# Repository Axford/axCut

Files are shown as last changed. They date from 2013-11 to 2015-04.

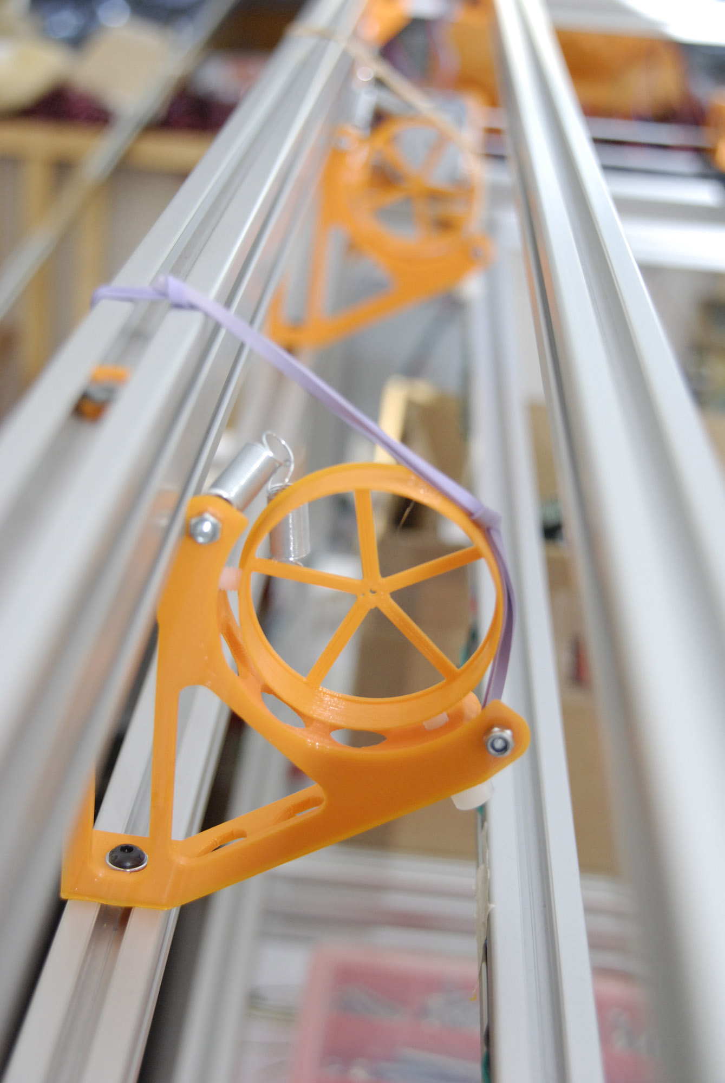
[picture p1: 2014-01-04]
images/wip_photos_1/_DSC1572.JPG

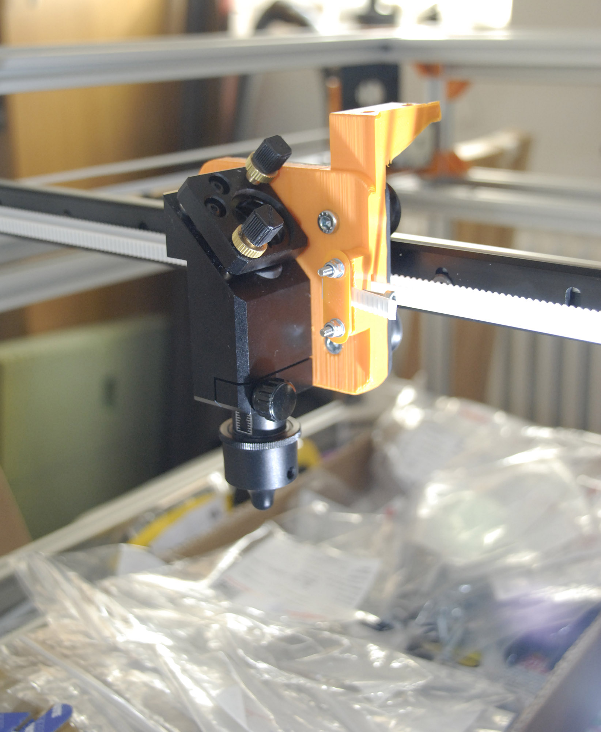
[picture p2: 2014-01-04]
images/wip_photos_1/_DSC1567.JPG

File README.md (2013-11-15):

axCut
=====

buildlog 2.x/Lasersaur inspired laser cutter

Clone the respository and open axCut.scad in latest version of OpenSCAD to view the WIP model.

Latest WIP image(s):

wip image

wip image

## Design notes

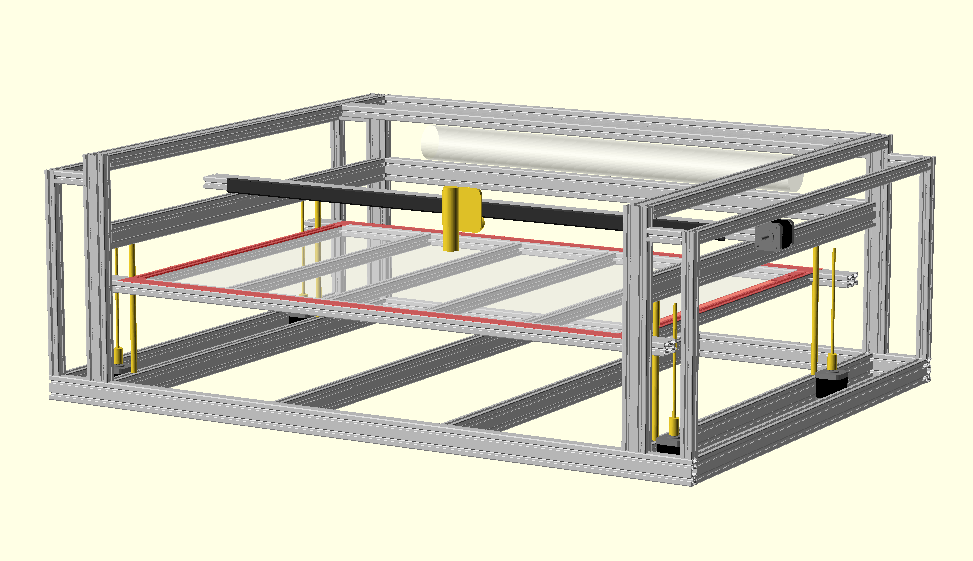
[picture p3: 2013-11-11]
images/axCut_wip1.png

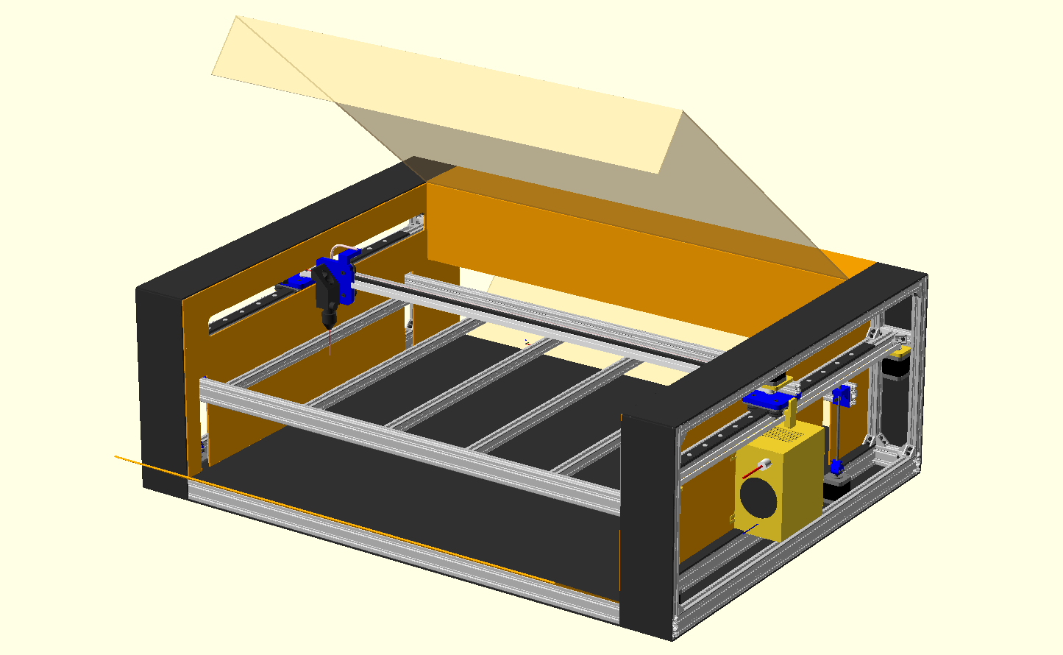
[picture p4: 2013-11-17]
images/axCut_wip8b.png

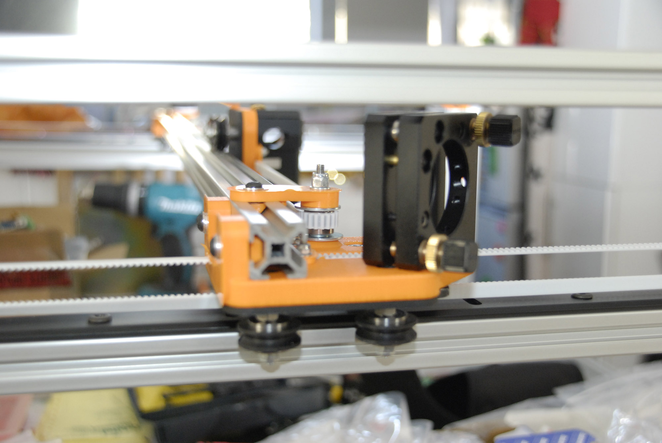
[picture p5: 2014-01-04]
images/wip_photos_1/_DSC1568.JPG

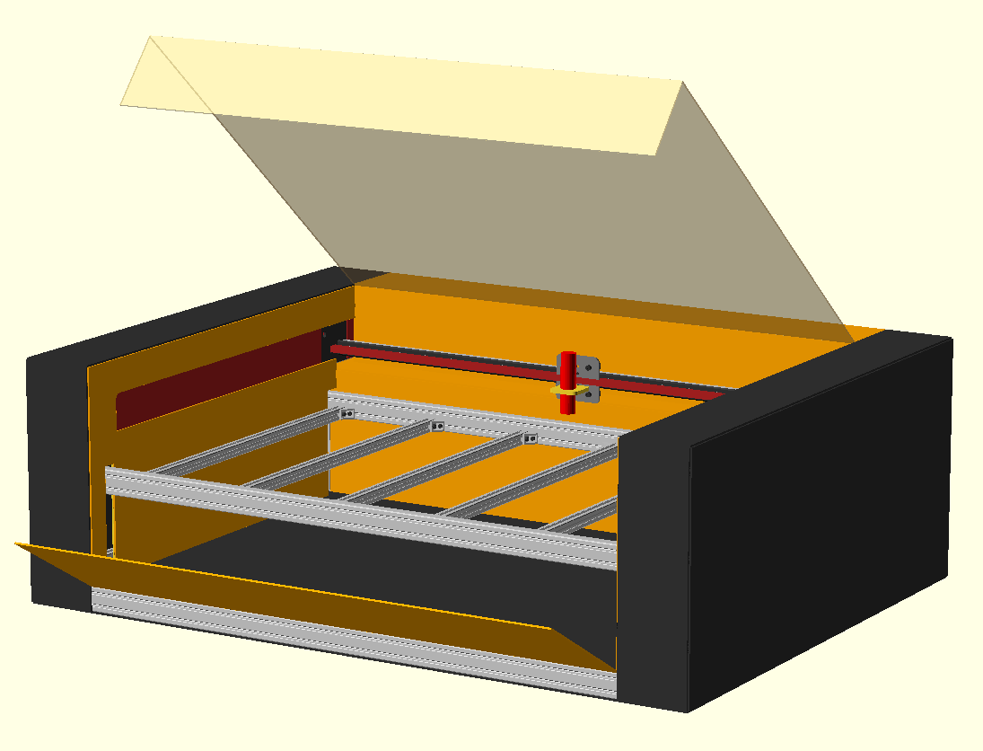
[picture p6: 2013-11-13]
images/axCut_wip4a.png

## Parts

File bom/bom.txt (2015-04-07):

Vitamins:
                  L                                        
                  a                                        
                  s                                        
                  e                                        
                  r                                        
                  b                                        
                  r                       Y                
              L   a                   Y   c                
              a   c                   c   a                
              s   k                   a   r                
              e   e                   r   r                
              r   t           X       r   i                
      C       a   a           c       i   a                
      l       s   s   T       a       a   g   Y            
      a       s   s   r       r       g   e           Z    
      d   F   e   e   o   X   r   X   e   r   i   Z   m    
      d   r   m   m   l   a   i   r   l   i   d   a   o   Z
  B   i   a   b   b   l   x   a   a   e   g   l   x   t   r
  e   n   m   l   l   e   i   g   i   f   h   e   e   o   o
  d   g   e   y   y   y   s   e   l   t   t   r   s   r   d
   |   |  8|   |   |   |   |   |   |   |   |   |   |   |   | 12 20x20TGusset:
   |   |  8|   |   |   |   |   |   |   |   |   |   |   |   |  8 20x40HeavyGusset:
   |   |   |   |   |   |   |   |  1|   |   |   |   |   |   |  1 Aluminium Extrusion BR_20x20 100mm
   |   |   |   |   |   |   |   |  1|   |   |   |   |   |   |  1 Aluminium Extrusion BR_20x20 1170mm
   |   |  8|   |   |   |   |   |   |   |   |   |   |   |   |  8 Aluminium Extrusion BR_20x20 350mm
  6|   |   |   |   |   |   |   |   |   |   |   |   |   |   |  6 Aluminium Extrusion BR_20x20 670mm
   |   |   |   |   | 10|   |   |   |   |   |   |   |   |   | 10 Aluminium Extrusion BR_20x20 710mm
   |   |  6|   |   |   |   |   |   |   |   |   |   |   |   |  8 Aluminium Extrusion BR_20x20 870mm
   |   |  3|   |   |   |   |   |   |   |   |   |   |   |   |  3 Aluminium Extrusion BR_20x20 990mm
  2|   |   |   |   |   |   |   |   |   |   |   |   |   |   |  2 Aluminium Extrusion BR_20x40 1100mm
   |   |   |   |   |  6|   |   |   |   |   |   |   |   |   |  6 Aluminium Extrusion BR_20x40 1160mm
   |   |  2|   |   |   |   |   |   |   |   |   |   |   |   |  2 Aluminium Extrusion BR_20x40 1200mm
   |   |   |   |   |  4|   |   |   |   |   |   |   |   |   |  4 Aluminium Extrusion BR_20x40 580mm
   |   |   |   |   |  4|   |   |   |   |   |   |   |   |   |  4 Aluminium Extrusion BR_20x40 670mm
   |   |  6|   |   |   |   |   |   |   |   |   |   |   |   |  6 Aluminium Extrusion BR_20x40 870mm
   |   |  1|   |   |   |   |   |   |   |   |   |   |   |   |  1 Aluminium Extrusion BR_20x40 990mm
 24|   |148|   |  4|   |   |   |  4|  2|  2|  4|   |   |   |196 Aluminium Extrusion Twist Nut
   |   |   |   |   |   |   |   |   |  2|   |  2|   |   |   |  4 Ball bearing 624 4mm x 13mm x 5mm
   |   |   |   |   |   |   |  8|   |   |  8|   |   |   |   | 16 Ball bearing 625_2RS 5mm x 16mm x 5mm
 12|   | 40|   |   |   |   |   |   |   |   |   |   |   |   | 52 BR20x20Gusset
   |   |   |   |   |   |   |   |  1|   |   |   |   |   |   |  1 Belt T2.5 x 6mm x 2185mm
   |   |   |   |   |   |   |   |   |   |   |   |   | 16|   | 16 M3 cap screw x 20mm
   |   |   |   |  4|   |   |   |  2|   |   |   |   |   |   | 10 M4 cap screw x 10mm
   |   |   |   |   |   |   |   |   |  2|  2|   |   |   |   |  4 M4 cap screw x 16mm
 24|   |148|   |   |   |   |   |  2|   |   |  4|   |   |   |182 M4 cap screw x 8mm
   |   |   |   |  4|   |   |   |   |   |   |   |   |   |   |  4 M5 cap screw x 20mm
   |   |   |   |   |   |   |  4|   |   |  4|   |   |   |   |  8 M5 cap screw x 25mm
   |   |   |   |   |   |   |  4|   |  4|  4|   |   |   |   | 12 M5 cap screw x 30mm
   |   |   |   |   |   |   |  4|   |   |  4|   |   |   |   |  8 DelrinVGrooveWheel:
   |   |   |   |   |   |   |  2|   |  4|  4|   |   |   |   | 10 M3 hex screw x 16mm
   |   |   |   |   |   |   |  2|   |   |   |   |   |   |   |  2 M3 hex screw x 25mm
   |   |   |   |   |   |   |  2|   |   |   |   |   |   |   |  2 M4 hex screw x 20mm
   |   |   |   |   |   |   |   |   |  1|   |  1|   |   |   |  2 M4 hex screw x 40mm
   |   |   |   |   |   |   |   | 20|   |   |   |   |   |   | 50 M5 low profile screw x 10mm
   |   |   |   |   |   |   |   |  1|   |   |   |   |  4|   |  7 NEMA17 x 47mm stepper motor
   |   |   |   |   |   |   |  4|   |  4|  4|   |   |   |   | 12 Nut M3
   |   |   |   |  4|   |   |   |   |   |   |   |   |   |   |  4 Nut M5
   |   |   |   |   |   |   |   |   |   |   |   |   | 16|   | 16 Nyloc nut M3
   |   |   |   |   |   |   |  2|   |  1|   |  1|   |   |   |  4 Nyloc nut M4
   |   |   |   |   |   |   |  4|   |   |  4|   |   |   |   |  8 Nyloc nut M5
   |   |   |   |   |   |   |  1|   |   |  1|   |   |   |   |  2 OpenRailPlate20:
   |   |   |   |   |   |   |  4|   |   |  4|   |   |   |   |  8 OpenRailSpacer:
   |   |   |   |   |   |   |   |  2|   |   |   |   |   |   |  2 Openrail1000:Openrail 1000mm
   |   |   |   |   |   |   |   |   |   |   |   |   |   |   |  4 Openrail750:Openrail 750mm
   |   |   |   |   |   |   |   | 20|   |   |   |   |   |   | 50 OpenrailTeeNut:
   |   |   |   |   |   |   |   |   |   |   |   |   |   |   |  1 Overall depth = ", 90
   |   |   |   |   |   |   |   |   |   |   |   |   |   |   |  1 Overall height = ", 38
   |   |   |   |   |   |   |   |   |   |   |   |   |   |   |  1 Overall width = ", 119
   |   |   |   |   |   |   |   |  4|   |   |   |   |   |   | 12 M3 pan screw x 8mm
   |   |   |   |   |   |   |   |  1|   |   |   |   |   |   |  3 T2.5x18 pulley 18 teeth
   |   |   |   |   |   |   |   |   |   |   |   |   |   |  2|  2 Smooth rod 10mm x 210mm
   |   |   |   |   |   |   |   |   |   |   |   |  2|   |   |  2 Rodlen", 21
   |   |   |   |   |   |   |   |   |   |   |   |   |  4|   |  4 Threaded rod M6 x 180mm
   |   |   |   |   |   |   |   |   |   |   |   |   |  4|   |  4 Neoprene tubing OD 8mm ID 5mm x 16mm
   |   |   |   |   |   |   |  4|  4|  4|  4|   |   | 16|   | 40 Washer M3 x 7mm x 0.5mm
   |   |  4|   |  4|   |   |  2|  4|  6|  2|  8|   |   |   | 38 Washer M4 x 9mm x 0.8mm
   |   |   |   |   |   |   |  4|   |   |  4|   |   |   |   |  8 Washer M5 x 10mm x 1mm
   |   |   |   |   |   |   |   |   |  2|   |  2|   |   |   |  4 Washer M5 x 20mm x 1.4mm
   |   |   |   |   |   |   |   |  4|   |   |   |   |   |   | 12 Star washer M3 x 0.5mm
   |   |   |   |   |   |   |   |   |   |   |   |   |   |   |  1 ", -38
   |   |   |   |   |   |   |   |   |   |   |   |   |   |   |  1 ", 37
   |   |   |   |   |   |   |   |   |   |   |   |   |   |   |  1 ", 42
   |   |   |   |   |   |   |   |   |   |   |   |   |   |   |  1 ", 50
   |   |   |   |   |   |   |   |   |   |   |   |   |   |   |  1 ", 8
   |   |   |   |   |   |   |  1|   |   |   |   |   |   |   |  1 laserHead:
   |   |   |   |   |   |   |   |  1|   |   |   |   |   |   |  2 laserMirror:
   |   |   |   |   |   |   |   |   |   |   |   |   |   |   |  1 ", 18

Printed:
   |   |   |   |   |   |   |   |   |   |   |   |   |   |   |  1 fixedMirrorHolder.stl
   |   |   |   |  2|   |   |   |   |   |   |   |   |   |   |  2 laserBracket.stl
   |   |   |   |   |   |   |  2|   |  2|  2|   |   |   |   |  6 xBeltClamp.stl
   |   |   |   |   |   |   |  1|   |   |   |   |   |   |   |  1 xBeltTensioner.stl
   |   |   |   |   |   |   |  1|   |   |   |   |   |   |   |  1 xCarriageBracket.stl
   |   |   |   |   |   |   |   |   |  1|   |   |   |   |   |  1 yCarriageBracketLeft.stl
   |   |   |   |   |   |   |   |   |   |  1|   |   |   |   |  1 yCarriageBracketRight.stl
   |   |   |   |   |   |   |   |   |   |   |  1|   |   |   |  1 y_idler_left.stl
   |   |   |   |   |   |   |   |   |   |   |  1|   |   |   |  1 y_idler_right.stl
   |   |   |   |   |   |   |   |   |   |   |   |   |  8|   |  8 z_coupling.stl

Sub-assemblies:
  1 bed
  1 cladding
  1 frame
  1 laserAssembly
  2 laserBracketAssembly
  1 trolley
  1 xAxis
  1 xCarriage
  1 xRail
  1 yCarriageLeft
  1 yCarriageRight
  1 y_idler_assembly
  1 zAxes
  4 zMotor
  2 zRod

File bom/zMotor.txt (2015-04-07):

zMotor:
Vitamins:
 16 M3 cap screw x 20mm
  4 NEMA17 x 47mm stepper motor
 16 Nyloc nut M3
  4 Threaded rod M6 x 180mm
  4 Neoprene tubing OD 8mm ID 5mm x 16mm
 16 Washer M3 x 7mm x 0.5mm

Printed:
  8 z_coupling.stl

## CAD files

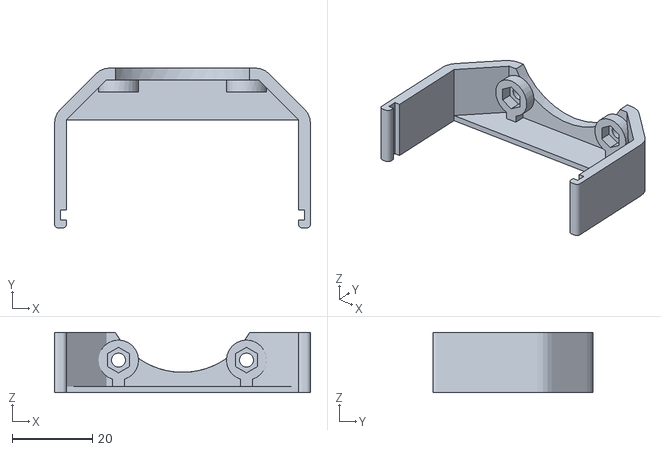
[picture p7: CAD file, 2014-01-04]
otherThings/Improved_ramps_fan.stl
64.0 x 40.0 x 15.0

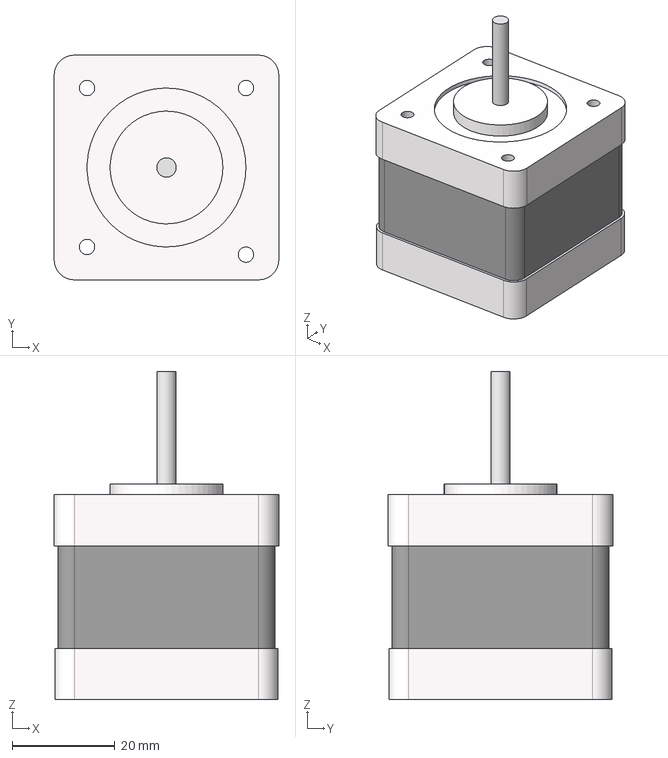
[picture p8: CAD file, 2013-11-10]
references/Nema17.stp
43.8 x 43.8 x 64.0 mm

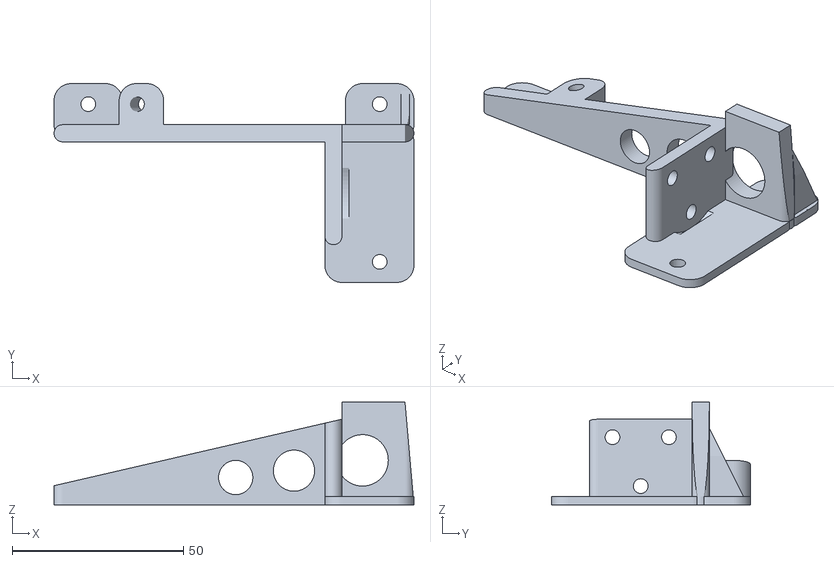
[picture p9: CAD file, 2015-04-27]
stl/upperFrameBracketForPistonLeft.stl
105.0 x 58.0 x 30.0

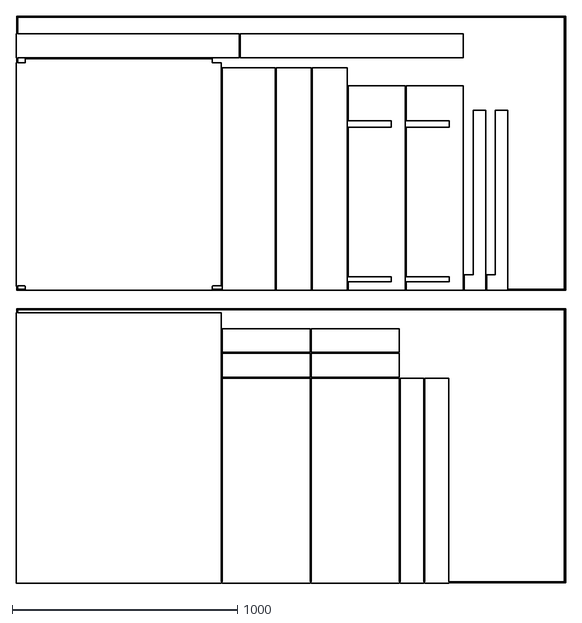
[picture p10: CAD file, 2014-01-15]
vitamins/claddingSheets.dxf
2440.0 x 2520.0

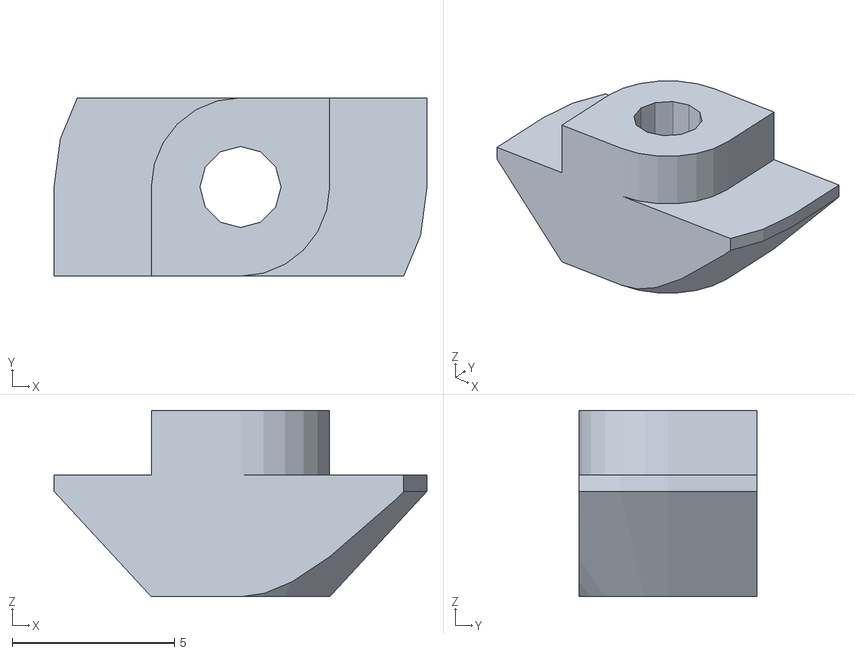
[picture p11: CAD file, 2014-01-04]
otherThings/hammerNut.stl
11.5 x 5.50 x 5.75

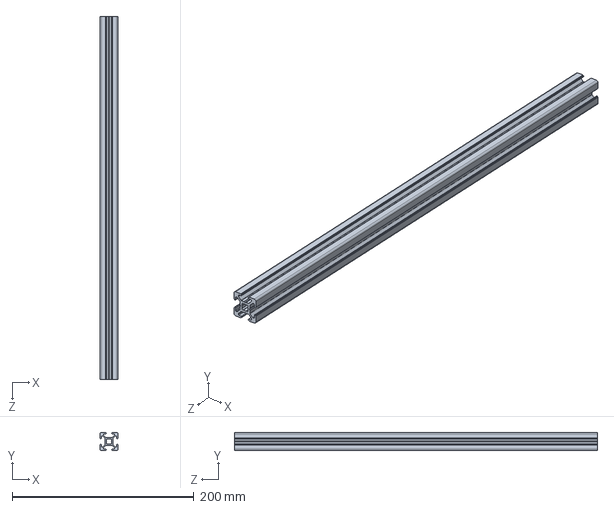
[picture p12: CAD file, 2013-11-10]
references/Rexroth-3 842 992 888_400MM.step
20.0 x 20.0 x 400.0 mm

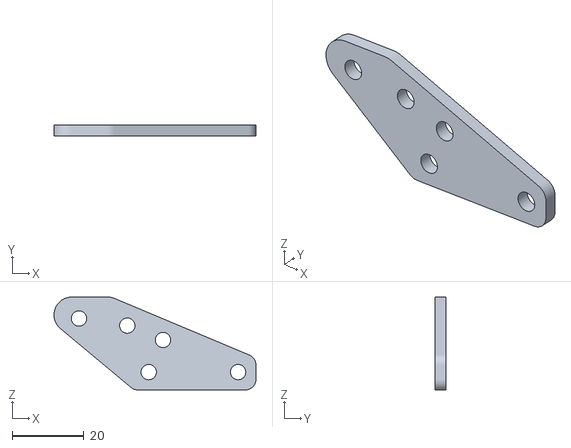
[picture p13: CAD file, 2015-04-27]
stl/ cableChainCarriageBracket.stl
56.5 x 3.00 x 26.0

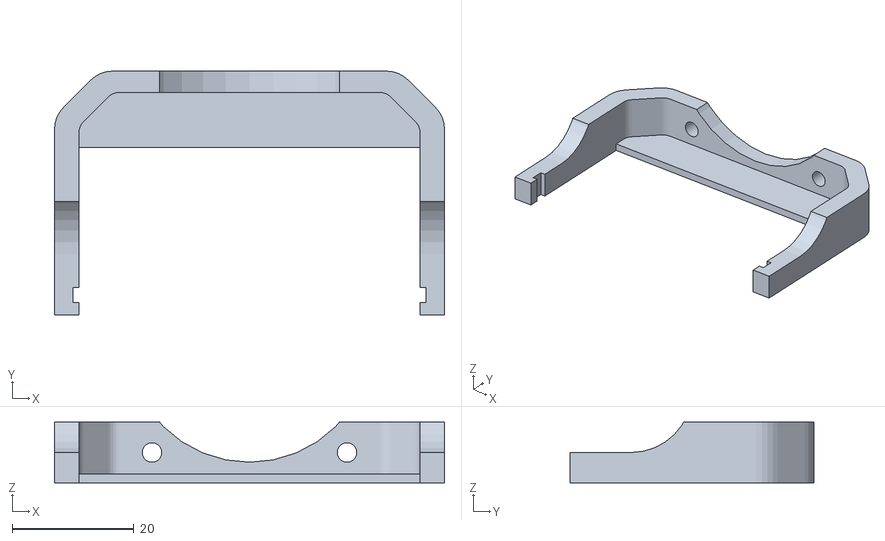
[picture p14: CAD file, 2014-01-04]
otherThings/rampsFanMount.stl
64.0 x 40.0 x 10.0

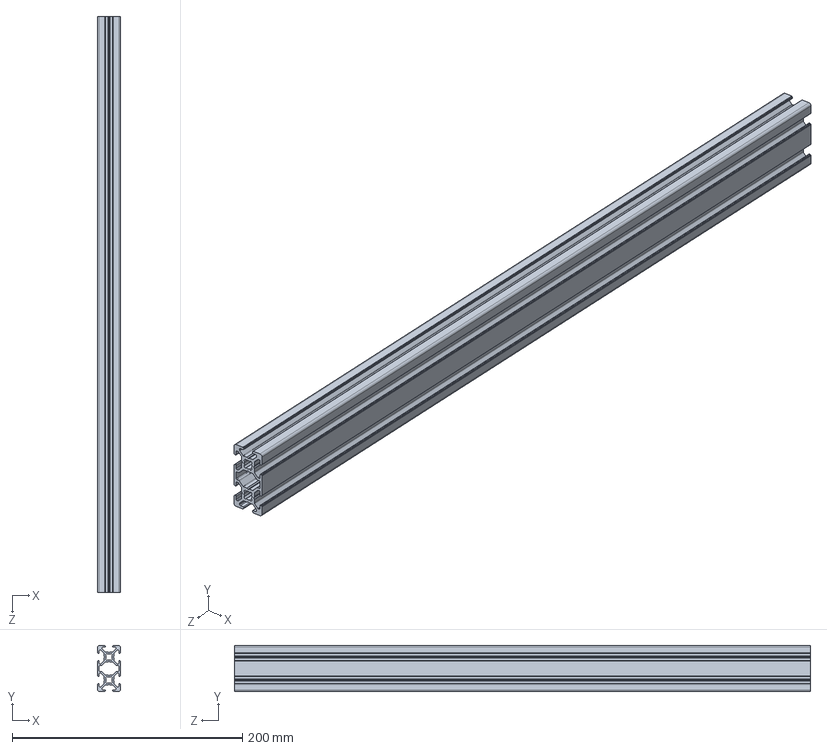
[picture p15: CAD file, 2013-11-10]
references/Rexroth-3 842 992 891_500MM.step
20.0 x 40.0 x 500.0 mm

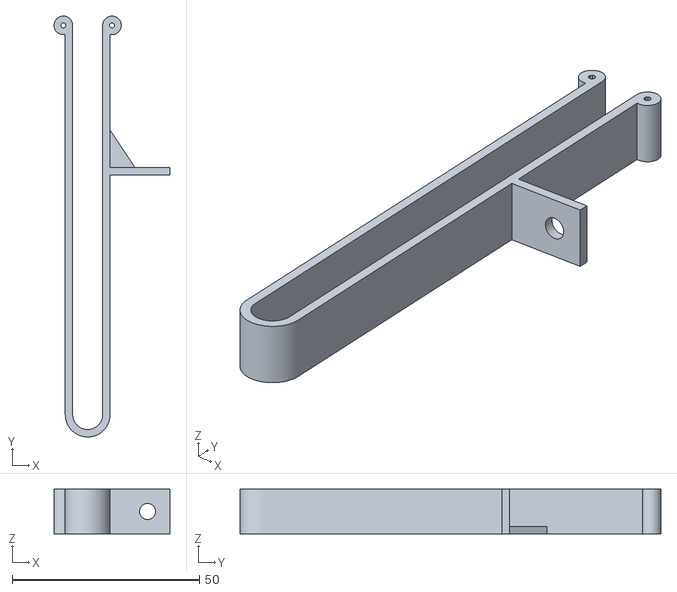
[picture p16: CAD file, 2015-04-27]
stl/airLineXBracket.stl
31.0 x 112.5 x 12.0

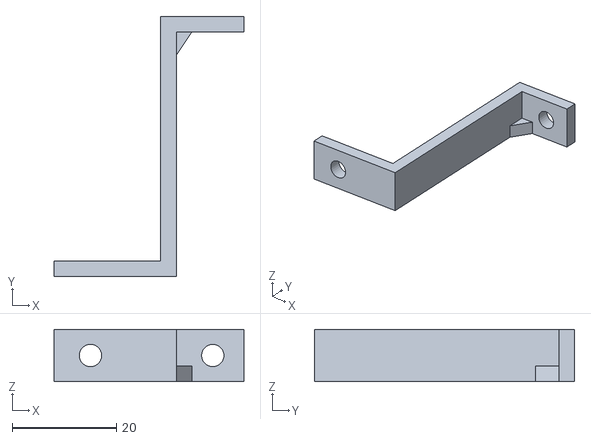
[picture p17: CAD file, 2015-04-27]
stl/cableChainXBracket.stl
36.5 x 50.0 x 10.0

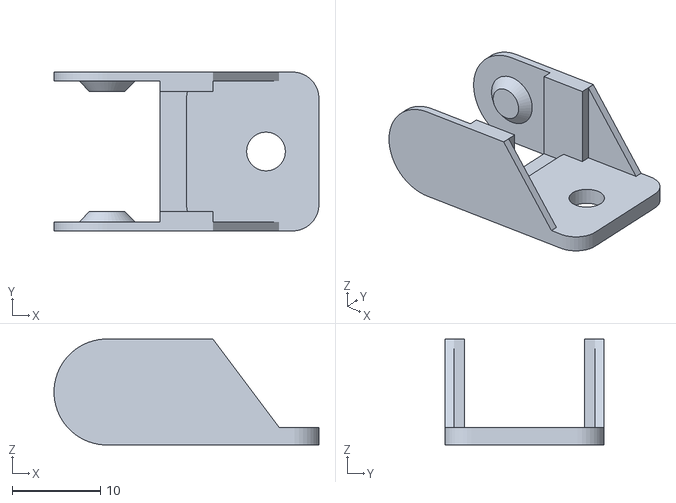
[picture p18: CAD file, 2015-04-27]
stl/cableChainFrameFixingMale.stl
30.0 x 18.0 x 12.0

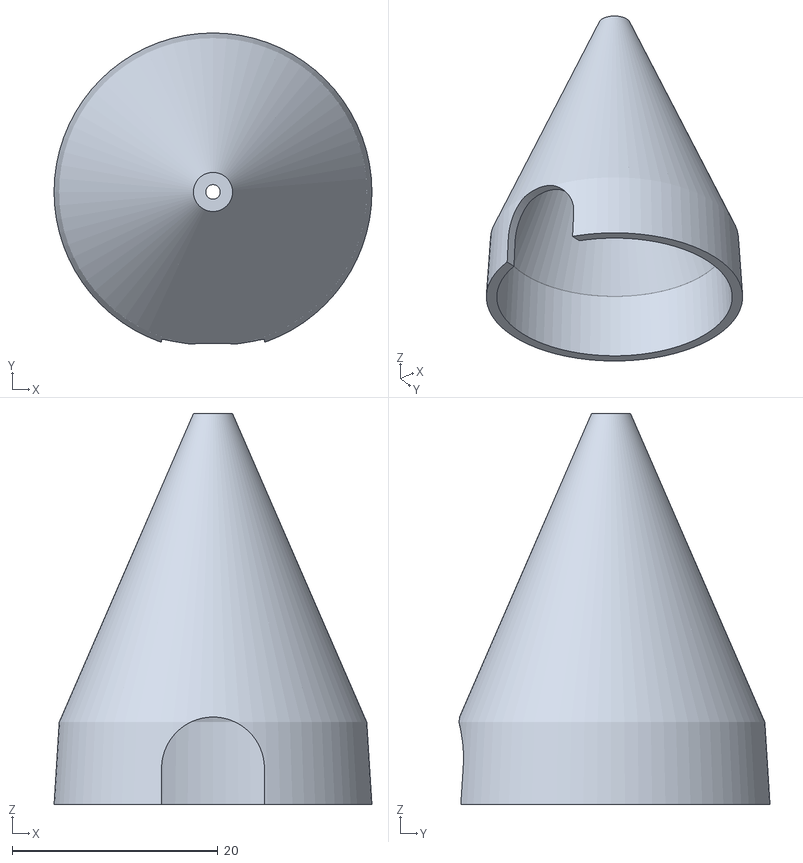
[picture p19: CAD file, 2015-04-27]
stl/laserNozzle.stl
30.9 x 30.2 x 38.0

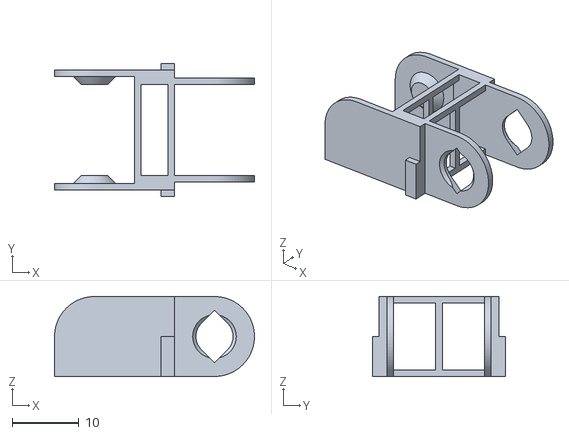
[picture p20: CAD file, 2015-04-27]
stl/cableChainLink.stl
30.0 x 20.0 x 12.0

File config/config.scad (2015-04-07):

//
// axCut
//
// GNU GPL v2
//
// Configuration file
//
bom = 0;                        // 0 no bom, 1 assemblies and stls, 2 vitamins as well
exploded = 0;                   // 1 for exploded view
simplify = false;    // reduces complexity of some parts, e.g. alu extrusions

show_jigs = true;               // show printed jigs required to build the machine
show_support = true;            // show support structures, must be set when generating STLs

debugConnectors = true;  //  show "attach" points

// Real-world colors for various parts & vitamins
use_realistic_colors = true;    // true for "real" colors, false for "distinct" colors (useful during design and for build instructions)
printed_plastic_color = "orange";
cable_strip_real_color = "fuchsia";
belt_real_color = "yellow";
bulldog_real_color ="black";

eta = 0.01;                     // small fudge factor to stop CSG barfing on coincident faces.
$fa = 5;
$fs = 0.5;

perim = 0.5;    // perim extrusion width for 0.2 or 0.3 layer height
layers = 0.3;
2perim = 2*perim;
4perim = 4*perim;

//
// Hole sizes
//
No2_pilot_radius = 1.7 / 2;       // self tapper into ABS
No4_pilot_radius = 2.0 / 2;       // wood screw into soft wood
No6_pilot_radius = 2.0 / 2;       // wood screw into soft wood

No2_clearance_radius = 2.5 / 2;
No4_clearance_radius = 3.5 / 2;
No6_clearance_radius = 4.0 / 2;

M2p5_tap_radius = 2.05 / 2;
M2p5_clearance_radius= 2.8 / 2;   // M2.5
M2p5_nut_trap_depth = 2.5;

M3_tap_radius = 2.5 / 2;
M3_clearance_radius = 3.3 / 2;
M3_nut_radius = 6.5 / 2;
M3_nut_trap_depth = 3;

M4_tap_radius = 3.3 / 2;
M4_clearance_radius = 2.2;
M4_nut_radius = 8.2 / 2;
M4_nut_trap_depth = 4;

M5_tap_radius = 4.2 / 2;
M5_clearance_radius = 5.3 / 2;
M5_nut_radius = 9.2 / 2;
M5_nut_depth = 4;

M6_tap_radius = 5 / 2;
M6_clearance_radius = 6.4 / 2;
M6_nut_radius = 11.6 / 2;
M6_nut_depth = 5;

M8_tap_radius = 6.75 / 2;
M8_clearance_radius = 8.4 / 2;
M8_nut_radius = 15.4 / 2;
M8_nut_depth = 6.5;

Z_screw_dia = 6;            // Studding for Z axis

//
// Feature sizes
//
default_wall = 4*perim;
thick_wall = 8*perim;

include <colors.scad>
include <utils.scad>
include <vitamins.scad>

endstop_wires    = [2, 1.4, "A"];   // 7 strands of 0.2
motor_wires      = [4, 1.4, "B"];
bed_wires        = [2, 2.8, "C"];   // 13A mains cable
fan_motor_wires  = [6, 1.4, "D"];   // fan and motor wires along top of gantry
two_motor_wires  = [8, 1.4,,"E"];   // Y and Z motors
thermistor_wires = endstop_wires;

endstop_wires_hole_radius = wire_hole_radius(endstop_wires);
motor_wires_hole_radius = wire_hole_radius(motor_wires);
two_motor_wires_hole_radius = wire_hole_radius(two_motor_wires);
fan_motor_wires_hole_radius = wire_hole_radius(fan_motor_wires);
bed_wires_hole_radius = wire_hole_radius(bed_wires);
thermistor_wires_hole_radius = wire_hole_radius(thermistor_wires);

cnc_sheets = false;                 // If sheets are cut by CNC we can use slots, etc instead of just round holes
base_nuts = false;                  // Need something under the base if using nuts
pulley_type = T2p5x18_metal_pulley;

Z_bearings = LM10UU;

X_motor = NEMA17;
Y_motor = NEMA17;
Z_motor = NEMA17;

X_belt = T2p5x6;
Y_belt = T2p5x6;

motor_shaft = 5;

Z_nut_radius = M6_nut_radius;
Z_nut_depth = M6_nut_depth;
Z_nut = M6_nut;

//
// Default screw use where size doesn't matter
//
cap_screw = M3_cap_screw;
hex_screw = M3_hex_screw;
//
// Screw for the frame and base
//
frame_soft_screw = No6_screw;               // Used when sheet material is soft, e.g. wood
frame_thin_screw = M4_cap_screw;            // Used with nuts when sheets are thin
frame_thick_screw = M4_pan_screw;           // Used with tapped holes when sheets are thick and hard, e.g. plastic or metal


screw_clearance_radius = screw_clearance_radius(cap_screw);
nut = screw_nut(cap_screw);
nut_radius = nut_radius(nut);
nut_trap_depth = nut_trap_depth(nut);
washer = screw_washer(cap_screw);

belt_clearance = 0.2;                   // clearance of belt clamp slots

Z_bar_dia = Z_bearings[2];

Y_idler_bearing = BB624;
X_idler_bearing = BB624;



///  

// OpenRail lengths  1000, 750

bedM = 30;  // bed margin, applied all round

bedW = 1000 - ORPlateWidth(ORPLATE20)/2 - 2*bedM;  //  adjusted to make full use of 1000mm rails
bedD = 750 - ORPlateWidth(ORPLATE20)/2 - 2*bedM;  // adjusted to make full use of 750mm rails

bedH = 300;
bedO = 70;  //bedOvershoot - applies to width only

bedWM = bedW + 2*bedM;  // with margins
bedDM = bedD + 2*bedM;

bedRibs = 6;  // number of ribs (along y axis)

bedVPos = 200;

zTravel = 210;

yCarriagePos = +bedD/2 -300;   // +-bedD
xCarriagePos = -bedW/2;    // +-bedW

xO = 60;  // xOvershoot
xVPos = 300;  // height of x axis above datum
yVPos = 270;  // height of y axis - to centreline of 2040 profile

rightW = 120;  // width of right casing, excludes outer panelling, runs from edge of bed margin
leftW = rightW;
backD = 150;  // depth of back casing
frontD = 40;  // depth of front casing

claddingC = 5;  // cladding clearance, inc thickness
claddingT = 3;  // cladding thickness


// frame centre lines, x/y relative to centre of bed, base of frame at z=0
//  centres lines lying in x axis
frameCX = [-bedDM/2 - frontD+10,
			bedDM/2 + claddingC + 10,  // back of bed
			bedDM/2 + claddingC + 60,  // behind x axis
			bedDM/2 + backD];

//  centres lines lying in y axis
frameCY = [-bedWM/2-rightW+10,  
		   -bedWM/2- 65,   // y rail
		   -bedWM/2 - claddingC-20,   
		   bedWM/2 + claddingC + 20,
		   bedWM/2 + 65,   // y rail
           bedWM/2 + leftW-10];     
           
//  centres lines lying in z axis
frameCZ = [20, 
		   zTravel + 50,   //  top of z rails	
           zTravel + 65,   //  y rails
		   zTravel + 170,   // outer corners
           zTravel + 170];  // top


showSealingBelts = false;

bedBearingOffset = 40;    // distance from centreline of front rail to centreline of rod
bedMotorYOffset = 40;  // distance from centreline of front/back rails to centreline of motor

showLaserBeam = true;


// trolley
trolleyHeight = 600;  // height from floor to top of trolley
trolleyDepth = 760;  // outer dimensions, excluding cladding
trolleyFloorClearance = 20;  // height above floor, to allow room for levelling feet


echo("Overall width = ", (frameCY[5]-frameCY[0]+16));
echo("Overall depth = ", (frameCX[3]-frameCX[0]+16));
echo("Overall height = ", (frameCZ[4]-frameCZ[0]+26));

for (i=[0:3])
	echo("X centres: ", frameCX[i]);


include <assemblies.scad>

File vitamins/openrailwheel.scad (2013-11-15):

// OpenRail delrin or steel wheel
// drawn by jdausilio/zeke7237

// from openbuilds drawings
openrailwheel_minRadius=18.75/2;
openrailwheel_coneMajorRadius=24.39/2;
openrailwheel_coneMinorRadius=9.77;
openrailwheel_width=10.23;
openrailwheel_vWidth=4.84;
openrailwheel_vGap=0.55;
openrailwheel_holeRadius=15.75/2;
openrailwheel_ridge=13.89/2;

module v_cone() {
	cylinder(r1=openrailwheel_coneMinorRadius,r2=openrailwheel_coneMajorRadius,h=openrailwheel_vWidth/2, center=true);
}

module openrail_eccentric_spacer() {
	vitamin(str("OpenRailEccentricSpacer:"));
	
	color(grey80)
		render()
		tube(8/2,5/2,5,$fn=6,center=false);
}

module openrail_spacer() {
	vitamin(str("OpenRailSpacer:"));
	
	color(grey80)
		render()
		tube(7/2,5/2,5,center=false);
}

module openrail_wheel() {
	vitamin(str("DelrinVGrooveWheel:"));

	color(grey20)
	render()
	difference() {
		union() {
			difference() {
				union() {
					cylinder(r=openrailwheel_minRadius, h=openrailwheel_width, center=true);
					translate([0,0,openrailwheel_vWidth/2+openrailwheel_vGap/2])cylinder(r=openrailwheel_coneMinorRadius, h=openrailwheel_vWidth, center=true);
					translate([0,0,-openrailwheel_vWidth/2-openrailwheel_vGap/2])cylinder(r=openrailwheel_coneMinorRadius, h=openrailwheel_vWidth, center=true);
					translate([0,0,openrailwheel_vGap/2+openrailwheel_vWidth/4])v_cone();
					translate([0,0,openrailwheel_vGap/2+openrailwheel_vWidth/4+openrailwheel_vWidth/2])rotate([180,0,0])v_cone();
					translate([0,0,-(openrailwheel_vGap/2+openrailwheel_vWidth/4)])rotate([180,0,0])v_cone();
					translate([0,0,-(openrailwheel_vGap/2+openrailwheel_vWidth/4+openrailwheel_vWidth/2)])v_cone();
				}
				cylinder(r=openrailwheel_holeRadius,h=20,center=true);
			}
			cylinder(r=openrailwheel_holeRadius+1,h=1,center=true);
		}
		cylinder(r=openrailwheel_ridge,h=5,center=true);
	}
}

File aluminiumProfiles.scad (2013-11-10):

//  Modules for the Bosch Rexroth series of aluminium profiles
//  Sourced from http://www.kjnltd.co.uk/
//  
//  Author - Damian Axford
//  Public Domain

use <moreShapes.scad>

eta = 0.01;


// Bore Types
BR_20x20_Bore = [5.5, 1.5, 7];

function aluProBore_r(boreType) = boreType[0]/2;
function aluProBore_outsetW(boreType) = boreType[1];
function aluProBore_outsetR(boreType) = boreType[2]/2;

// Core Types
BR_20x20_Core = [9,2,0.75];

function aluProCore_w(coreType) = coreType[0];
function aluProCore_keyW(coreType) = coreType[1];
function aluProCore_keyD(coreType) = coreType[2];

//Corner Types
BR_20x20_Corner = [20, 7, 1.5, 0.5, 4];

// Side Types  - for closed slots
BR_20x20_Side = [20, 1.5];

// Side Styles
BR_0 = [0,0,0,0];
BR_1S = [0,1,1,1];
BR_2S = [0,1,0,1];
BR_3S = [0,1,0,0];
BR_2SA = [1,1,0,0];

// Profiles - combination of elements

BR_20x20 = [BR_20x20_Bore, BR_20x20_Core, BR_20x20_Corner, BR_20x20_Side, BR_0, 1, 1];
BR_20x20_1S = [BR_20x20_Bore, BR_20x20_Core, BR_20x20_Corner, BR_20x20_Side, BR_1S, 1, 1];
BR_20x20_2S = [BR_20x20_Bore, BR_20x20_Core, BR_20x20_Corner, BR_20x20_Side, BR_2S, 1, 1];
BR_20x20_3S = [BR_20x20_Bore, BR_20x20_Core, BR_20x20_Corner, BR_20x20_Side, BR_3S, 1, 1];
BR_20x20_2SA = [BR_20x20_Bore, BR_20x20_Core, BR_20x20_Corner, BR_20x20_Side, BR_2SA, 1, 1];

BR_20x40 = [BR_20x20_Bore, BR_20x20_Core, BR_20x20_Corner, BR_20x20_Side, BR_0, 1, 2];

BR_20x60 = [BR_20x20_Bore, BR_20x20_Core, BR_20x20_Corner, BR_20x20_Side, BR_0, 1, 3];

BR_20x80 = [BR_20x20_Bore, BR_20x20_Core, BR_20x20_Corner, BR_20x20_Side, BR_0, 1, 4];

//twistLockNutType

BR_20x20_TwistLockNut = [5.8,11.3,4,0.8,1.5];


module aluProBore(boreType, $fn=16) {
	union() {
		circle(r=aluProBore_r(boreType));
	
		intersection() {
			circle(r=aluProBore_outsetR(boreType));
			for (i=[0:3]) 
				rotate([0,0,i*90 + 45]) 	
				square([aluProBore_outsetR(boreType)*2,aluProBore_outsetW(boreType)], center=true);
		}
	}
}


module aluProCore(coreType) {
	w = aluProCore_w(coreType);
	keyW = aluProCore_keyW(coreType);
	keyD = aluProCore_keyD(coreType);

	difference() {
		square([w,w],center=true);

		// remove keys
		for (i=[0:3]) 
			rotate([0,0,i*90])
			translate([w/2,0,0])
			polygon([[eta,keyW/2], 
                      [-keyD,0], 
                      [eta,-keyW/2]]); 
	}
}


module aluProCorner(cornerType, $fn=8) {
	// xy corner
	w1 = cornerType[0];
	w2 = cornerType[1];
	t = cornerType[2];
	cham = cornerType[3];
	w3 = cornerType[4];	

	union() {	
		// radial arm
		rotate([0,0,45]) translate([0,-t/2,0]) square([w1/2+t,t]);

		// outer radius
		translate([w1/2-t,w1/2-t,0]) circle(r=t);

		// corner block
		translate([w1/2-w3,w1/2-w3]) square([w3-t+eta,w3-t+eta]);

		// returns
		for (i=[0,1]) mirror([i,i,0]) {
			translate([w1/2-w2,w1/2-t,0]) square([w2-t,t-cham]);
			translate([w1/2-w2+cham,w1/2-cham-eta,0]) square([w2-t-cham,cham+eta]);
		}
	}
}

module aluProSide(sideType) {
	// x side
	w = sideType[0];
	t = sideType[1];
	translate([w/2-t-eta,-w/4,0]) square([t+eta,w/2]);	
}

module aluProHollow(cornerType) {
	// x hollow
	w1 = cornerType[0];
	t = cornerType[2];
	w3 = cornerType[4];	

	translate([w1/2,0]) square([2*w3 - 2*t, w1 - 2*t],center=true);
}

// TSlot - to be unioned onto a printed part for engaging tightly with the aluprofile
//  same centre and orientation as a full profile section, x+ side
// protrudes eta beyond external boundary of section to allow for union
// requires linear_extrude'ing
module aluProTSlot(profileType, $fn=8) {
	//BR_20x20_Corner = [20, 7, 1.5, 0.5, 4];
	//BR_20x20_Core = [9,2,0.75];
	
	coreType = profileType[1];
	cornerType = profileType[2];
	 
	w1 = cornerType[0];
	w2 = cornerType[1];
	t = cornerType[2];
	cham = cornerType[3];
	w3 = cornerType[4];	

	tol = 0.5;  // mm tolerance, total per gap

	slotW = w1- 2*w2 - tol;
	slotD = (w1 - coreType[0]) / 2 - tol;
	slotOffset = coreType[0]/2 + tol;
	
	wingW = w1 - 2*w3 - 4*tol;
	wingInset = t + tol/2;

	union() {	
		// central block
		translate([slotOffset,-slotW/2,0]) square([slotD+eta, slotW]);
	
		// wings
		for (i=[0,1]) mirror([0,i,0]) {
			polygon(points=[[slotOffset,slotW/2],[w1/2-w3/2-tol,wingW/2],[w1/2-wingInset,wingW/2],[w1/2-wingInset, slotW/2]], paths=[[0,1,2,3]]);
		}
	}
}

// TSlotLug - to be unioned onto a printed part for engaging tightly with the aluprofile slot
//  same centre and orientation as a full profile section, x+ side
// protrudes eta beyond external boundary of section to allow for union
// NB: solid part
module aluProTSlotLug(profileType, l=5, $fn=8) {
	//BR_20x20_Corner = [20, 7, 1.5, 0.5, 4];
	//BR_20x20_Core = [9,2,0.75];
	
	coreType = profileType[1];
	cornerType = profileType[2];
	 
	w1 = cornerType[0];
	w2 = cornerType[1];
	t = cornerType[2];
	cham = cornerType[3];
	w3 = cornerType[4];	

	tol = 0.5;  // mm tolerance, total per gap

	slotW = w1- 2*w2 - tol;
	slotD = (w1 - coreType[0]) / 2 - tol;
	slotD2 = l < slotD ? l : slotD;
	slotOffset = coreType[0]/2 + tol;
	
	wingW = w1 - 2*w3 - 4*tol;
	wingInset = t + tol/2;

	union() {	
		// central block
		translate([slotOffset,-slotW/2,0]) square([slotD2+eta, slotW]);
	}
}



module aluProBasicSection(profileType) {
	difference() {
		union() {
			aluProCore(profileType[1]);
			
			for (i=[0:3]) rotate([0,0,i*90]) {
				aluProCorner(profileType[2]);

				if (profileType[4][i] == 1)
					aluProSide(profileType[3]);
			}
		}
		aluProBore(profileType[0]);
	}
}

module aluProSection(profileType) {
	x = profileType[5];
	y = profileType[6];
	w = profileType[3][0];
	sx = -(x-1)*w/2;
	sy = -(y-1)*w/2;

	difference() {
		union() {
			for (i=[0:x-1])
				for (j=[0:y-1])
					translate([sx + w * i, sy + w * j,0]) aluProBasicSection(profileType);
			
			// fill-in sides
			if (y > 1)
				for (i=[0:y-2])
					for (j=[0,1]) 
						mirror([j,0,0])
							translate([sx + (x-1) * w/2, sy + i*w + w/2,0])
								aluProSide(profileType[3]);
		}

		// remove hollows
		if (y > 1)
			for (i=[0:y-2])
				for (j=[0,1]) 
					mirror([j,0,0])
						translate([sx + (x-1) * w/2, sy + i*w,0])
							rotate([0,0,90]) aluProHollow(profileType[2]);
	}
		
}

module aluProExtrusion(profileType, l=100, center=false) {
	color([0.8,0.8,0.8])
	    translate([0,0,center?-l/2:0]) 
		linear_extrude(height=l)
		aluProSection(profileType, center);
}

//BR_20x20_TwistLockNut = [5.8,11.3,4,0.8,1.5];
// aligned such that the origin is level with the surface of the profile when the nut is locked
module aluProTwistLockNut(tlnt) {
	color("silver")
	translate([0,0,-tlnt[2] -tlnt[3] - (tlnt[4] - tlnt[3])]) 
	difference() {
		union() {
			translate([0,0,tlnt[2]-0.5-eta]) cube([tlnt[1],tlnt[0],1+2*eta],center=true);
			translate([0,0,(tlnt[2]-1)/2]) rotate([90,0,0]) trapezoidPrism(tlnt[1],tlnt[0],tlnt[2]-1,-(tlnt[1] - tlnt[0])/2,tlnt[0],center=true);
			
			translate([0,0,tlnt[3]/2 + tlnt[2]-eta]) cube([tlnt[0],tlnt[0],tlnt[3] + eta],center=true);
		}
	
		translate([0,0,-1]) cylinder(h=20, r=tlnt[2]/2, $fn=8);
	}
}

*arrangeShapesOnGrid(showLocalAxes=true) {
	aluProExtrusion(BR_20x20, l=80, center=true);
	aluProExtrusion(BR_20x20_1S, l=50);
	aluProExtrusion(BR_20x20_2S, l=50);
	aluProExtrusion(BR_20x20_3S, l=70);
	aluProExtrusion(BR_20x20_2SA, l=70);

	aluProExtrusion(BR_20x40, l=70, center=false);
	aluProExtrusion(BR_20x60, center=true);
	rotate([0,0,35]) aluProExtrusion(BR_20x80, center=false);
}

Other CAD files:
stl/upperFrameBracketLeft.stl
stl/exhaustCoupling.stl
stl/upperFrameBracketForPiston.stl
stl/upperFrameBracketForHingeLeft.stl
axCut.scad
assemblies/CableChainv3.scad
assemblies/bed.scad
assemblies/cableChain.scad
assemblies/cladding.scad
assemblies/cooling.scad
assemblies/electronics.scad
assemblies/exhaust.scad
assemblies/frame.scad
assemblies/laser.scad
assemblies/trolley.scad
assemblies/xAxis.scad
assemblies/xLimitSwitch.scad
assemblies/yAxes.scad
assemblies/yIdler.scad
assemblies/z-coupling.scad
assemblies/zAxes.scad
assemblies/zLimitSwitch.scad
ball-bearings.scad
bom.scad
claddingSheets.scad
config/assemblies.scad
config/bom.scad
config/colors.scad
config/utils.scad
config/vitamins.scad
curvedPipe.scad
microbore.scad
microswitch.scad
otherThings/uploads-0c-e6-5b-80-5a-RAMPS+Fan+Mount.scad
otherThings/uploads-5d-4e-60-6e-da-T-Nut.scad
partdev.scad
partdev2.scad
screws.scad
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

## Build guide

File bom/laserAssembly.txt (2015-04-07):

laserAssembly:
Vitamins:

Printed:

Sub-assemblies:
  2 laserBracketAssembly

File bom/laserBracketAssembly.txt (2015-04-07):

laserBracketAssembly:
Vitamins:
  4 Aluminium Extrusion Twist Nut
  4 M4 cap screw x 10mm
  4 M5 cap screw x 20mm
  4 Nut M5
  4 Washer M4 x 9mm x 0.8mm

Printed:
  2 laserBracket.stl

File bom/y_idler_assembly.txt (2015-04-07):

y_idler_assembly:
Vitamins:
  4 Aluminium Extrusion Twist Nut
  2 Ball bearing 624 4mm x 13mm x 5mm
  4 M4 cap screw x 8mm
  1 M4 hex screw x 40mm
  1 Nyloc nut M4
  8 Washer M4 x 9mm x 0.8mm
  2 Washer M5 x 20mm x 1.4mm

Printed:
  1 y_idler_left.stl
  1 y_idler_right.stl

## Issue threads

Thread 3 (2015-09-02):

Where's the license

burdickjp, 2015-09-02:
Your laser cutter looks awesome, but I don't see a license anywhere on the repo. Am I missing something?

I use the CERN license following OSHWA guidelines for my open source hardware projects.
http://www.ohwr.org/projects/cernohl/wiki

Axford, 2015-09-02:
thanks ... and forgot to add one when I first uploaded the repo - treat as public domain!

Will upload a statement to that effect at some point

thanks
D

burdickjp, 2015-09-02:
If it is no different to you, use a license which guarantees derivative work is also free by adopting an open hardware license. Public domain does not guarantee this, and can be detrimental to the community.
Just upload the cern license and continue about your day. You won't see the difference, but we (the community) will!
http://www.ohwr.org/attachments/2388/cern_ohl_v_1_2.txt

Axford, 2015-09-04:
I'm fairly indifferent...  CERN license sounds ok, will add when near a suitable computer

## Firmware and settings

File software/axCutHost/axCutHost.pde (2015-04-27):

import processing.serial.*;
import controlP5.*;
import java.util.Arrays;
import java.io.BufferedWriter;
import java.io.FileWriter;

ControlP5 cp5;
PFont f;

DropdownList dlSerialPorts;
StringList serialLog;
Serial port; 

JSONObject config;

float x=0, y=0, z=0;

String lastCmd = "";
String lastCmdRaw = "";
int lastLineNo = 0;
int resendCount = 0;

StringList sendBuffer = new StringList();

boolean cts = true;
boolean resend = false;

void saveConfig() {
  // save connection string
  saveJSONObject(config, "config.json");
}

void stop() {
  saveConfig(); 
  Disconnect(0);

  super.stop();
}


void setup() {
  size(700, 400, P3D);
  f = createFont("Arial", 11, true); 

  try {
    config = loadJSONObject("config.json");
  } 
  catch(Exception e) {
  }

  cp5 = new ControlP5(this);

  // Configure Serial Ports Dropdown
  // -------------------------------
  dlSerialPorts = cp5.addDropdownList("dlSerialPorts")
    .setPosition(5, 25)
      .setWidth(200)
        ;
  dlSerialPorts.captionLabel().set("Choose a Serial Port");
  customize(dlSerialPorts);
  // Get list of ports
  dlSerialPorts.addItems(Serial.list());

  if (config != null) {
    int i = Arrays.asList(Serial.list()).indexOf(config.getString("port"));  
    dlSerialPorts.setValue(i);
  }

  // Connect button
  cp5.addButton("Connect")
    .setPosition(220, 5)
      .setSize(50, 20)
        ;

  // Disconnect button
  cp5.addButton("Disconnect")
    .setPosition(280, 5)
      .setSize(50, 20)
        ;


  // home
  cp5.addButton("Home")
    .setPosition(340, 5)
      .setSize(50, 20)
        ;


  // Send
  cp5.addButton("SendCommand")
    .setPosition(400, 5)
      .setSize(50, 20)
        ;
        
        
  // Store
  cp5.addButton("Store")
    .setPosition(460, 5)
      .setSize(50, 20)
        ;
        
        
   // PlayBack
  cp5.addButton("PlayBack")
    .setPosition(520, 5)
      .setSize(50, 20)
        ;
        
   // Abort
  cp5.addButton("Abort")
    .setPosition(580, 5)
      .setSize(50, 20)
        ;
        
  // Z
  cp5.addSlider("Z")
    .setValue(0.0)
      .setRange(0.0, 300.0)
        .setPosition(220, 170)
          .setSize(200, 20)
            ; 

  cp5.addTextfield("LastCommand")
    .setPosition(220, 200)
      .setSize(400, 20)
        .setFont(createFont("arial", 11))
          .setAutoClear(false)
            ;

  cp5.addTextfield("NewCommand")
    .setPosition(220, 250)
      .setSize(400, 20)
        .setFont(createFont("arial", 11))
          .setAutoClear(false)
            ;
            
  cp5.addTextfield("ResendErrors")
    .setPosition(220, 290)
      .setSize(40, 20)
        .setFont(createFont("arial", 11))
          .setAutoClear(false)
            ;
            
  // Arm button
  cp5.addButton("ArmLaser")
    .setPosition(220, 40)
      .setSize(50, 20)
        ;
  
  // Disarm button
  cp5.addButton("DisarmLaser")
    .setPosition(280, 40)
      .setSize(50, 20)
        ;
        
  // Test fire button
  cp5.addButton("TestFire")
    .setPosition(340, 40)
      .setSize(50, 20)
        ;


  // Configure serialLog
  serialLog = new StringList();
  serialLog.append("Log");
  serialLog.append("---");
}

public void Connect(int theValue) {
  if (dlSerialPorts.getValue() >= 0) {
    String c = Serial.list()[int(dlSerialPorts.getValue())];
    port = new Serial(this, c, 115200);
    port.bufferUntil(10);  // line feed

    config.setString("port", c);
    saveConfig();
  }
}

public void Disconnect(int theValue) {
  if (port != null) {
    port.dispose();
    port = null;
    
    sendBuffer.clear();
  }
}

public void SendCMD(String c) {
  if (port != null) {
    serialLog.append(c + "\r\n");
    appendTextToFile("serial.log",c + "\r\n");
    cts = false; // reset by receiving an ok
    println("sending: "+c + "\r\n");
    port.write(c + "\r\n"); 
    lastCmd = c;
    cp5.get(Textfield.class, "LastCommand").setText(c);
  }
}

public void QueueCMD(String c) {
   sendBuffer.append(c); 
}

public void Home(int v) {
  QueueCMD("G28 XY");
  QueueCMD("G28 Z");
}


public void Z(float v) {
  z = v;
}

public void SendCommand(int v) {
  QueueCMD(cp5.get(Textfield.class, "NewCommand").getText());
}

public void NewCommand(String s) {
  QueueCMD(cp5.get(Textfield.class, "NewCommand").getText());
}

public void Store(int v) {
   appendTextToFile("playback.gcode",lastCmd);
}

public String AddCRCXOR(int line, String c) {
  String cmd = "N"+line +c;
  
  int cs = 0;
  for(int i = 0; i < cmd.length(); i++)
    cs = cs ^ cmd.charAt(i);
  cs &= 0xff;  // Defensive programming...
  
  return cmd + "*"+cs;
}

int CRC8(String s) {
  int crc = 0x00;
  int len = s.length();
  int i = 0;
  while (len-- > 0) {
    int extract = 0xFF & (int) s.charAt(i);
    i++;
    for (int tempI = 8; tempI > 0; tempI--) {
      int sum = (crc ^ extract) & 0x01;
      crc >>= 1;
      if (sum > 0) {
        crc ^= 0x8C;
      }
      extract >>= 1;
    }
  }
  return crc;
}


static int auchCRCHi[] = {
0x00, 0xC1, 0x81, 0x40, 0x01, 0xC0, 0x80, 0x41, 0x01, 0xC0, 0x80, 0x41, 0x00, 0xC1, 0x81,
0x40, 0x01, 0xC0, 0x80, 0x41, 0x00, 0xC1, 0x81, 0x40, 0x00, 0xC1, 0x81, 0x40, 0x01, 0xC0,
0x80, 0x41, 0x01, 0xC0, 0x80, 0x41, 0x00, 0xC1, 0x81, 0x40, 0x00, 0xC1, 0x81, 0x40, 0x01,
0xC0, 0x80, 0x41, 0x00, 0xC1, 0x81, 0x40, 0x01, 0xC0, 0x80, 0x41, 0x01, 0xC0, 0x80, 0x41,
0x00, 0xC1, 0x81, 0x40, 0x01, 0xC0, 0x80, 0x41, 0x00, 0xC1, 0x81, 0x40, 0x00, 0xC1, 0x81,
0x40, 0x01, 0xC0, 0x80, 0x41, 0x00, 0xC1, 0x81, 0x40, 0x01, 0xC0, 0x80, 0x41, 0x01, 0xC0,
0x80, 0x41, 0x00, 0xC1, 0x81, 0x40, 0x00, 0xC1, 0x81, 0x40, 0x01, 0xC0, 0x80, 0x41, 0x01,
0xC0, 0x80, 0x41, 0x00, 0xC1, 0x81, 0x40, 0x01, 0xC0, 0x80, 0x41, 0x00, 0xC1, 0x81, 0x40,
0x00, 0xC1, 0x81, 0x40, 0x01, 0xC0, 0x80, 0x41, 0x01, 0xC0, 0x80, 0x41, 0x00, 0xC1, 0x81,
0x40, 0x00, 0xC1, 0x81, 0x40, 0x01, 0xC0, 0x80, 0x41, 0x00, 0xC1, 0x81, 0x40, 0x01, 0xC0,
0x80, 0x41, 0x01, 0xC0, 0x80, 0x41, 0x00, 0xC1, 0x81, 0x40, 0x00, 0xC1, 0x81, 0x40, 0x01,
0xC0, 0x80, 0x41, 0x01, 0xC0, 0x80, 0x41, 0x00, 0xC1, 0x81, 0x40, 0x01, 0xC0, 0x80, 0x41,
0x00, 0xC1, 0x81, 0x40, 0x00, 0xC1, 0x81, 0x40, 0x01, 0xC0, 0x80, 0x41, 0x00, 0xC1, 0x81,
0x40, 0x01, 0xC0, 0x80, 0x41, 0x01, 0xC0, 0x80, 0x41, 0x00, 0xC1, 0x81, 0x40, 0x01, 0xC0,
0x80, 0x41, 0x00, 0xC1, 0x81, 0x40, 0x00, 0xC1, 0x81, 0x40, 0x01, 0xC0, 0x80, 0x41, 0x01,
0xC0, 0x80, 0x41, 0x00, 0xC1, 0x81, 0x40, 0x00, 0xC1, 0x81, 0x40, 0x01, 0xC0, 0x80, 0x41,
0x00, 0xC1, 0x81, 0x40, 0x01, 0xC0, 0x80, 0x41, 0x01, 0xC0, 0x80, 0x41, 0x00, 0xC1, 0x81,
0x40
} ;
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

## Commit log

2013-11-10 initial commit
    key file is axCut.scad
    [2Dshapes.scad, aluminiumProfiles.scad, axCut.scad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]
2013-11-10 frame sketched out with major components
    [Nema17.stp, Rexroth-3 842 992 888_400MM.step, Rexroth-3 842 992 891_500MM.step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]
2013-11-11 reworked file structure to mimic Mendel90
    [2Dshapes.scad, aluminiumProfiles.scad, axCut.scad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]
2013-11-11 started openrail plate vitamin
    [axCut.scad, colors.scad, config.scad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]
2013-11-11 reworked openrail, added openrail plates and fittings
    [ball-bearings.scad, openrail.scad, openrailplates.scad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]
2013-11-11 added 20x20 gussets
    [aluminiumProfiles.scad, openrail.scad, openrailplates.scad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]
2013-11-11 added Gussets shortcut module
    [aluminiumProfiles.scad, partdev.scad]
2013-11-11 frame updates
    [axCut.scad, partdev.scad]
2013-11-12 further work on alu profile utility functions and reworked frame assembly
    [aluminiumProfiles.scad, axCut.scad, config.scad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]
2013-11-12 added rails to x and y axes
    [axCut.scad, config.scad, openrailplates.scad]
2013-11-12 rails and drive belts
    simplified rail and frame arrangement, added placeholders for steppers,
    drive belts and idlers to test fit
    [aluminiumProfiles.scad, axCut.scad, config.scad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]
2013-11-13 started cladding
    [axCut.scad, config.scad]
2013-11-13 further updates to frame/rail design and adding of y sealing belts
    [colors.scad, config.scad, moreShapes.scad]
2013-11-14 restructured around assemblies, started refining zAxes
    [axCut.scad, bed.scad, cladding.scad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]
2013-11-14 further zAxes refinement
    [bed.scad]
2013-11-14 New WIP images
    [axCut.scad]
2013-11-14 started modelling laser optics and xCarriageBracket
    [bed.scad, config.scad, laserOptics.scad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]
2013-11-15 tweaked file structure, updated readme
    [Nema17.stp, Rexroth-3 842 992 888_400MM.step, Rexroth-3 842 992 891_500MM.step]
2013-11-15 started modelling mirrors and laser path
    [assemblies.scad, axCut.scad, config.scad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]
2013-11-15 further refinements to optics, rail configuration, frame dimensions
    [cladding.scad, colors.scad, config.scad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]
2013-11-15 started modelling laser power supply
    [axCut.scad, laserPowerSupply.scad, partdev.scad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]
2013-11-16 finished laser power supply model, added into frame
    [axCut.scad, cladding.scad, laserPowerSupply.scad]
2013-11-16 added airline to xAxis with test animation
    [axCut.scad, cableChain.scad, config.scad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]
2013-11-16 updates to laser beams, xbracket
    [laserOptics.scad, partdev.scad, xAxis.scad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]
2013-11-17 bom generation mostly functioning, further refinement on xCarriage and supporting elements
    [aluminiumProfiles.scad, bom.scad, colors.scad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]
2013-11-17 draft cladding layouts
    [2Dshapes.scad, cladding.scad, config.scad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]
2013-11-18 Completed 20x20TGusset model
    [AluProParts.scad, partdev.scad, screws.scad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]
2013-11-18 finalised cladding and updated BOM
    [axCut.scad, bom.scad, cladding.scad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]
2013-11-18 replaced 65mm 20x20 with 20x20TGusset parts
    [AluProParts.scad, axCut.scad, frame.scad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]
2013-11-18 Added heavy duty gusset model, fitted into base frame
    [AluProParts.scad, aluminiumProfiles.scad, frame.scad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]
2013-11-18 updated BOM
2013-11-18 changed z axes nuts to M6
    [bed.scad]
2013-12-10 refining and making parts
    [20x20TGusset.stl, 20x40HeavyGusset.stl, AluProParts.scad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]
2013-12-15 finalising xAxisMotorPlate for print
    [AluProParts.scad, attach.scad, axCut.scad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]
2013-12-21 x and y axes complete
    [AluProParts.scad, assemblies.scad, attach.scad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]
2013-12-21 fixedMirrorHolder designed
    [fixedMirrorHolder.stl, laser.scad, partdev.scad]
2013-12-22 added laserBrackets
    [config.scad, laser.scad, laserBracket.stl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]
2013-12-22 finishing laserBrackets and laserCalibrator
    [2Dshapes.scad, AluProParts.scad, axCut.scad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]
2013-12-27 refinind square nut carrier
    [AluProParts.scad, partdev.scad, squareNutCarrier with lock.stl]
2014-01-04 axes complete, optics complete, onto water cooling
    [20x20PrintedGusset.stl, AluProParts.scad, Improved_ramps_fan.stl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]
2014-01-05 working on watercooling parts
    [cooling.scad, coolingTubeGrommet.stl, coolingTubeReturnElbow.stl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]
2014-01-09 cooling parts finished
    [axCut.scad, cooling.scad, coolingFlowSensorBracket.stl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]
2014-01-10 refining optics
    redesigned fixedMirrorHolder to be more rigid and use less plastic.
    Added laserCollars to spread load from nylon screws and reduce risk of
    cracking the tube.
    [fixedMirrorHolder.stl, laser.scad, laserCollar.stl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]
2014-01-10 further revision of the fixedMirrorHolder and laserCollar, start on s/w
    [fixedMirrorHolder.stl, laser.scad, laserCollar.stl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]
2014-01-13 software experiments
    [cooling.scad, coolingTubeBracket.stl, coolingTubeThermistorBracket.stl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]
2014-01-15 tweak to cladding
    [claddingSheets.dxf, claddingSheets.scad]
2014-02-17 added 2nd y motor to model
    [yAxes.scad]
2015-04-27 Various part revisions, host controller
    [cableChainCarriageBracket.stl, StockMetal.scad, airLineXBracket.stl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]
2015-08-03 fix case mismatch for use on case-sensitive OS
    [vitamins.scad]
